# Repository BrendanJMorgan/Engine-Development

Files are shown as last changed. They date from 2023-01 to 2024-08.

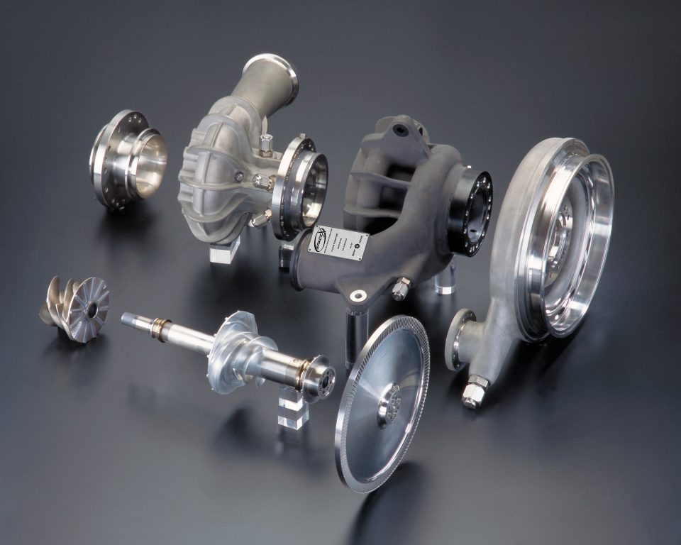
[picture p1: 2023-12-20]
Documents/Merlin-Turbopump-A-JPG1-960x768.jpg

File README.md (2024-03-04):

# Engine-Development
LOx-Ethanol Gas Generator Cycle Rocket Engine Analysis

This folder centers around designing a gas generator cycle rocket engine. By default the propellants are liquid oxygen and ethanol, though it should be fairly easy to change the code to other common propellants. The solidworks CAD reflects design parameters outputted by the MATLAB code. 

To use, open the main.m file and run. Engine target parameters can be adjusted right from this file. For example, target thrust, chamber pressure, OF ratio, and some basic dimensions for both the main combustion chamber (CC) and gas generator (GG) can be changed here.

The MATLAB code requires CoolProp integration to run. CoolProp is a python library with a MATLAB wrapper. The easiest installation method I know of can be followed from this video: https://www.youtube.com/watch?v=XvR10Fjph7U
The code also reuires NASA's CEAM to run, though this is already included in the folder so no further action should be required. NASA CEAM is approved for both domestic and international release.

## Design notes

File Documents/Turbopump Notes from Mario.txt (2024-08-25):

e pumps mostly
gillic textbook (julic? yulic?)
	roughness, specific speed
diffuser angles, stalling, loss vs angles
fuel inducer assuming impinging on leading edge
shrouding inducers is not that big deal, nor are somewhat wide tip clearances

ross (python library for rotordynamics)
pressurize seal with gn2, but two separated packing seals
zero leakage seal

x or o bearing arrangement

wave spring (soft preload better than hard preload)
tight tolerance on radial part of impeller (sealing) - 1 mm or less maybe
	other clearances can be wider
20-30% efficiency on turbine, maybe higher if load/power coefficient is lower

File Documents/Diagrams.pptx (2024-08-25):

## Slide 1

Spin Axis

rshaft

rinner

rrms

Flow In

reye

rexit

p1

p2

weye

Impeller Curve

Shroud Curve

p3

p4

wexit

Flow Out

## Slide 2

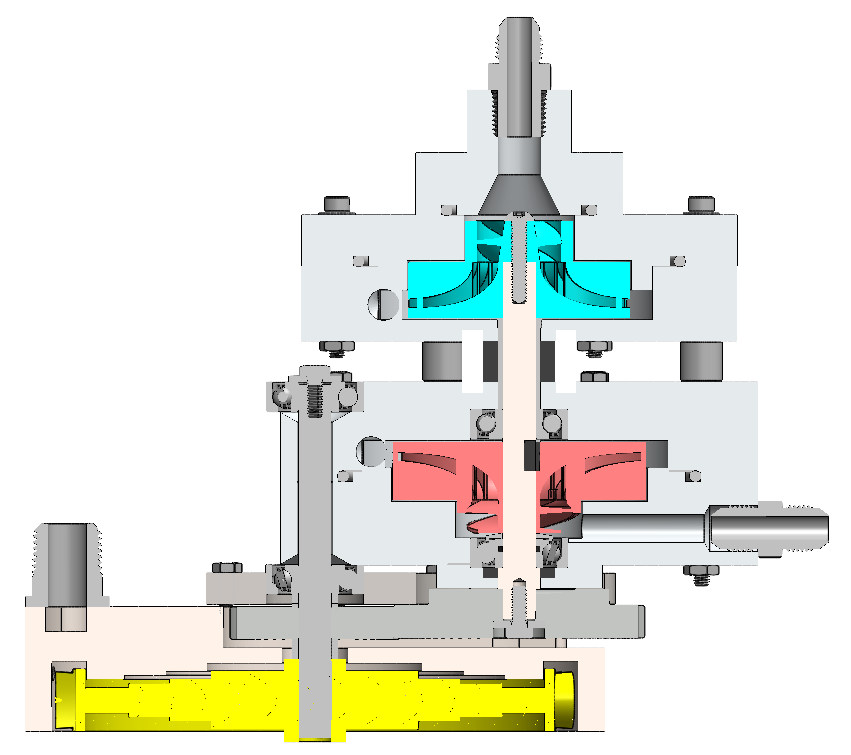
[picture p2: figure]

Ox Inlet

Oxidizer Pump

Bearings

Fuel Pump

Gas Inlet

Fuel Inlet

Manifold

Gears

Rotor

Turbine

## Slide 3

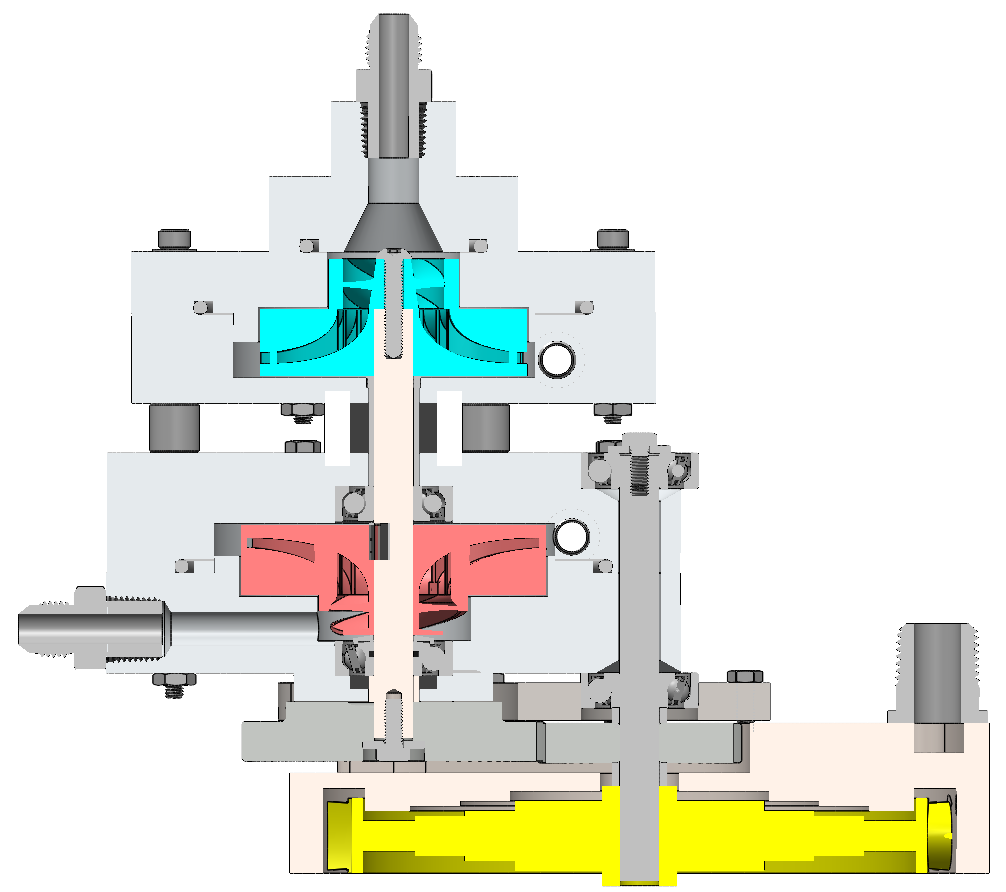
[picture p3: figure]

Ox Inlet

Oxidizer Pump

Outlets

Fuel Pump

Bearings

Fuel Inlet

Mounting Plate

Gas Inlet

Gears

Manifold

Turbine

Rotor

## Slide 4

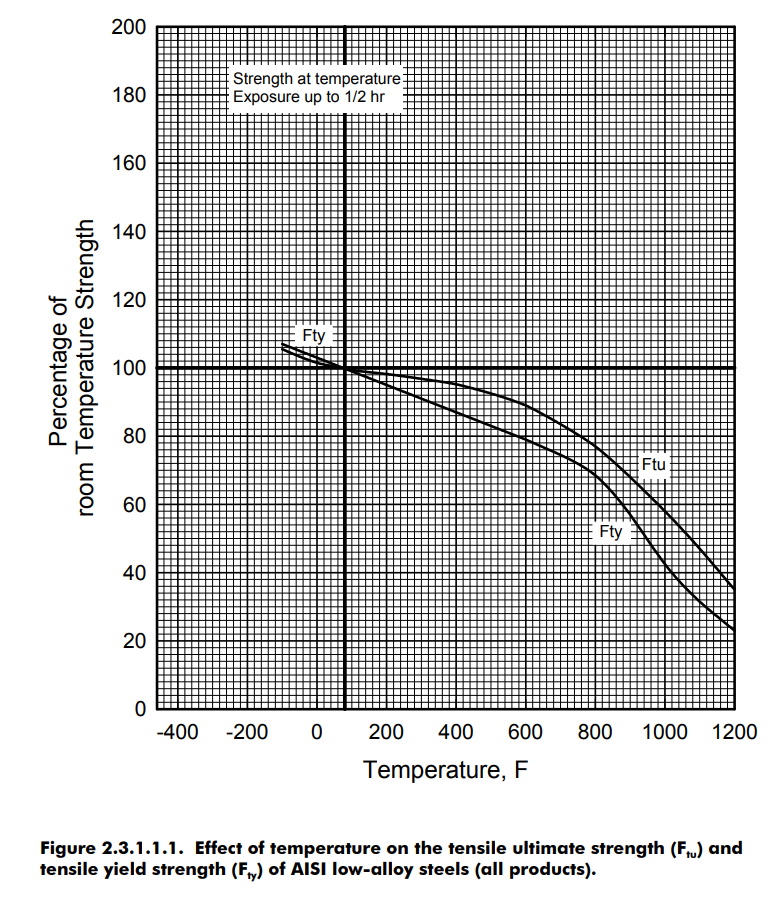
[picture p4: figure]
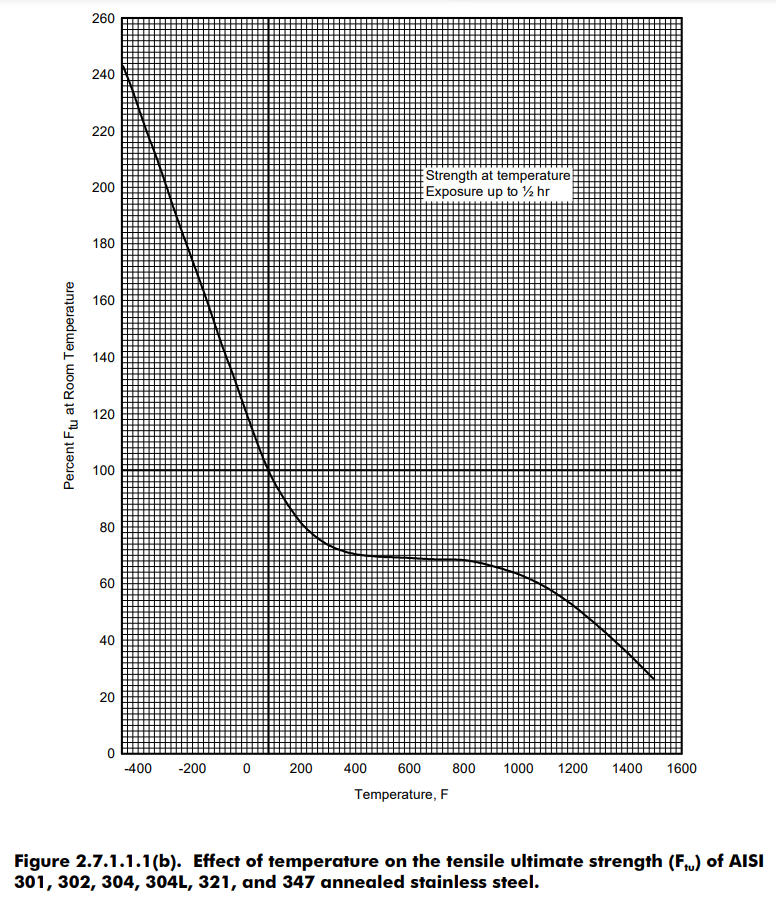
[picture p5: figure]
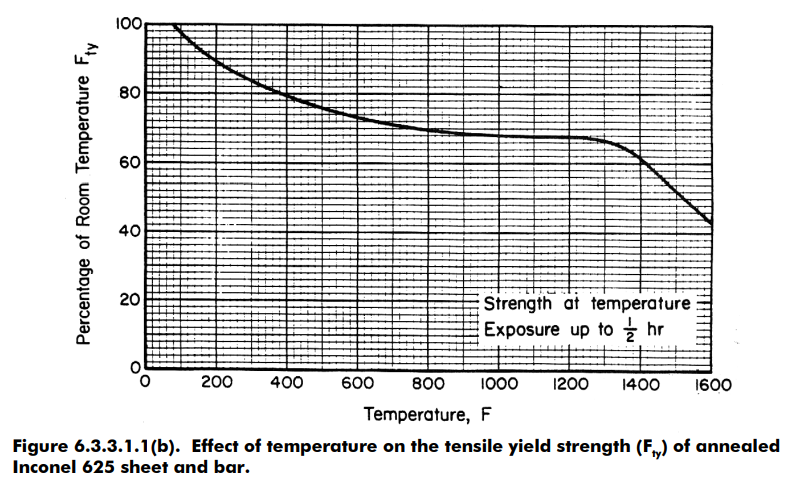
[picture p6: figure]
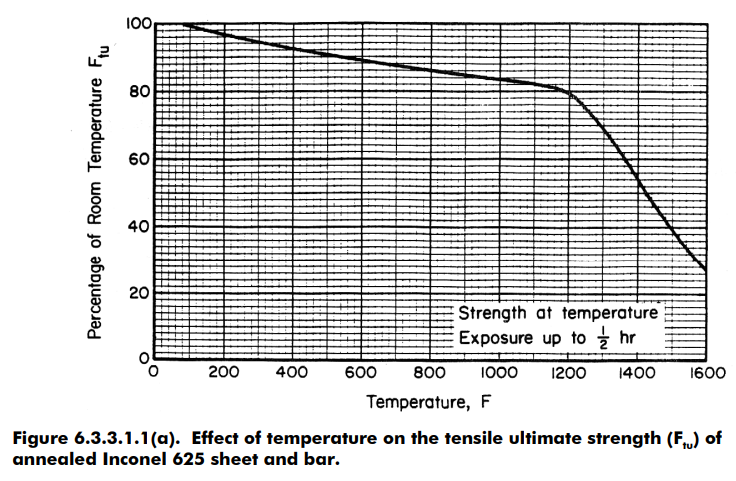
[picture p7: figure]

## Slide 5

rexit

p3

βoutlet

p4

p2

βinlet

reye

p1

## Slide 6

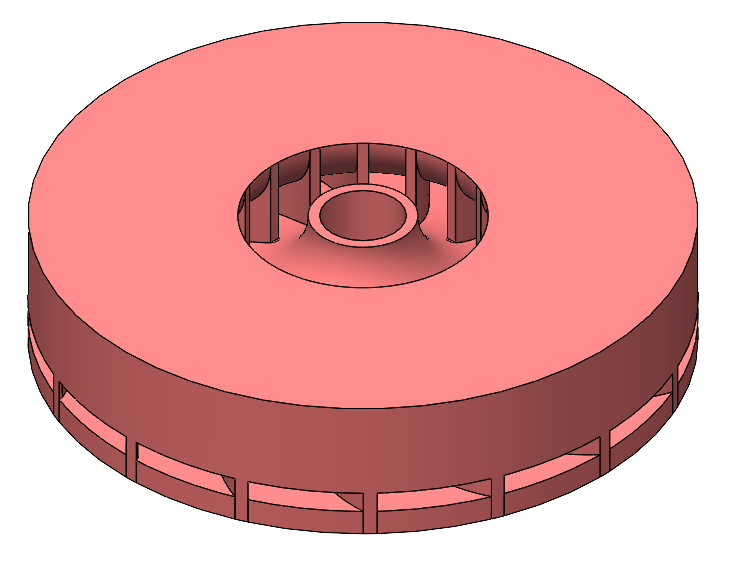
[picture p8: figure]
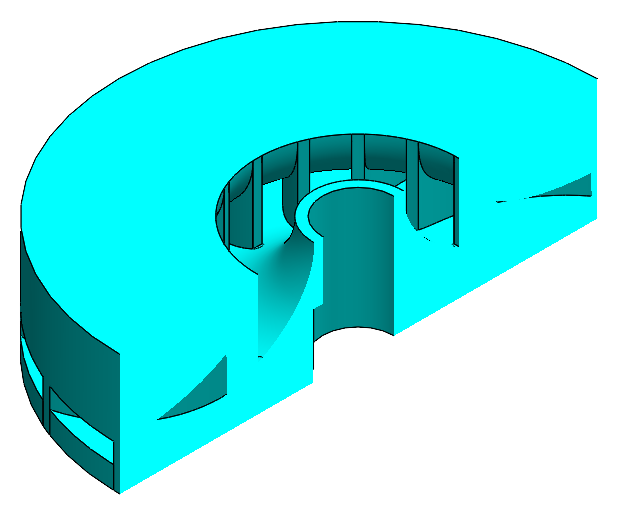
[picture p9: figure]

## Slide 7

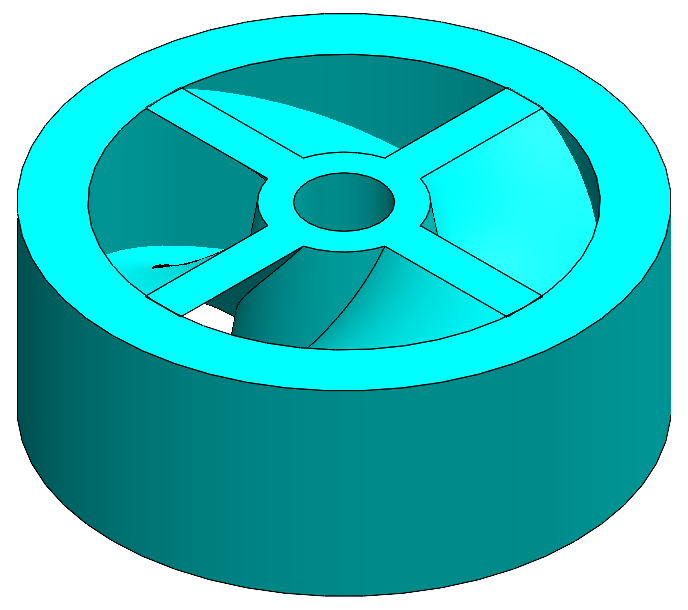
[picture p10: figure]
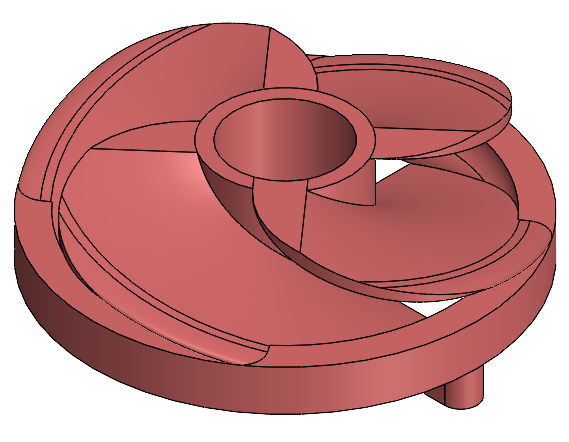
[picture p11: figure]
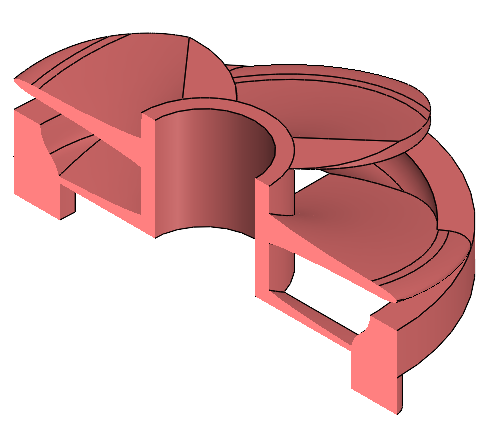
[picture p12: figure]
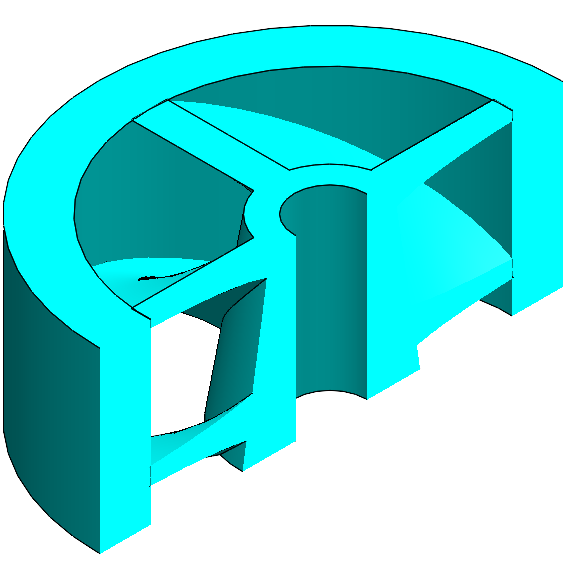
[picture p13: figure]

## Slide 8

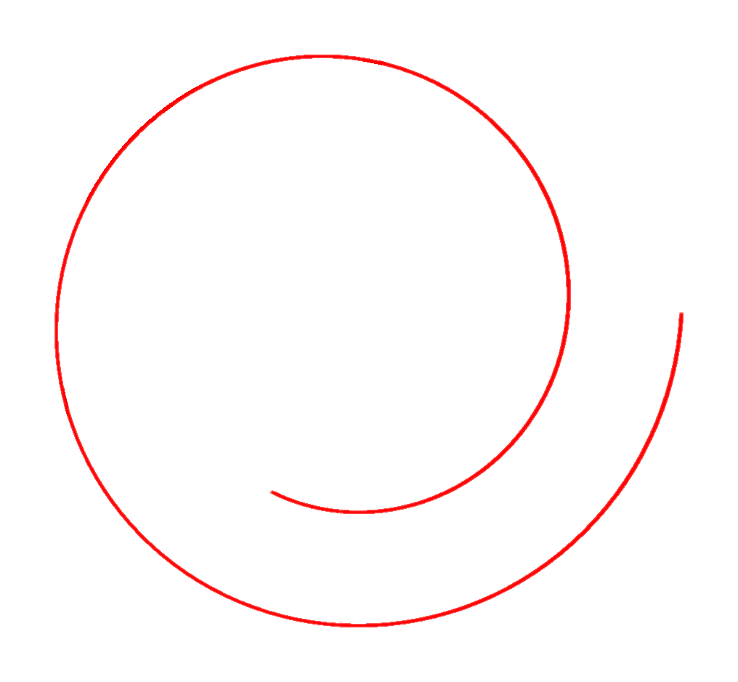
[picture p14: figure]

Impeller

routlet

rexit

Circular Cross Section, Aoutlet

Square Cross Section, Aoutlet

rtongue

ttongue

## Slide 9

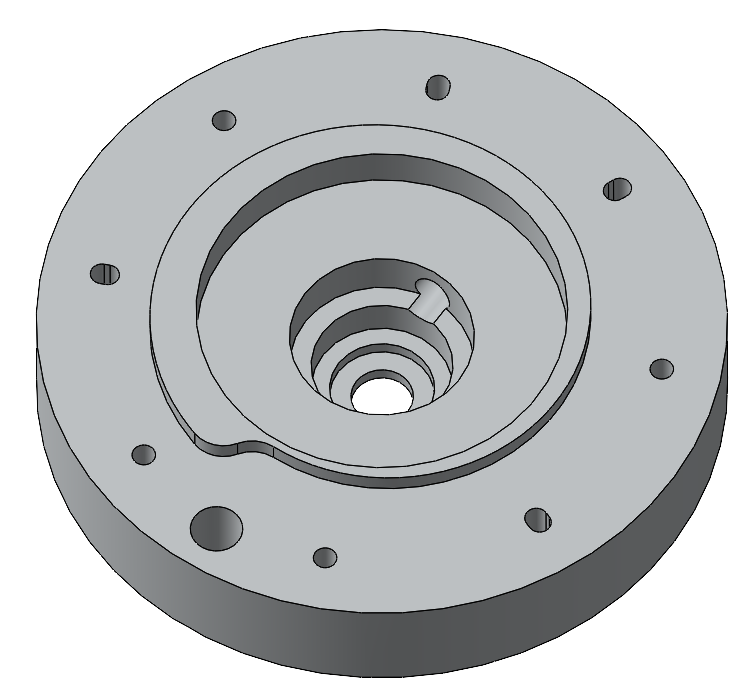
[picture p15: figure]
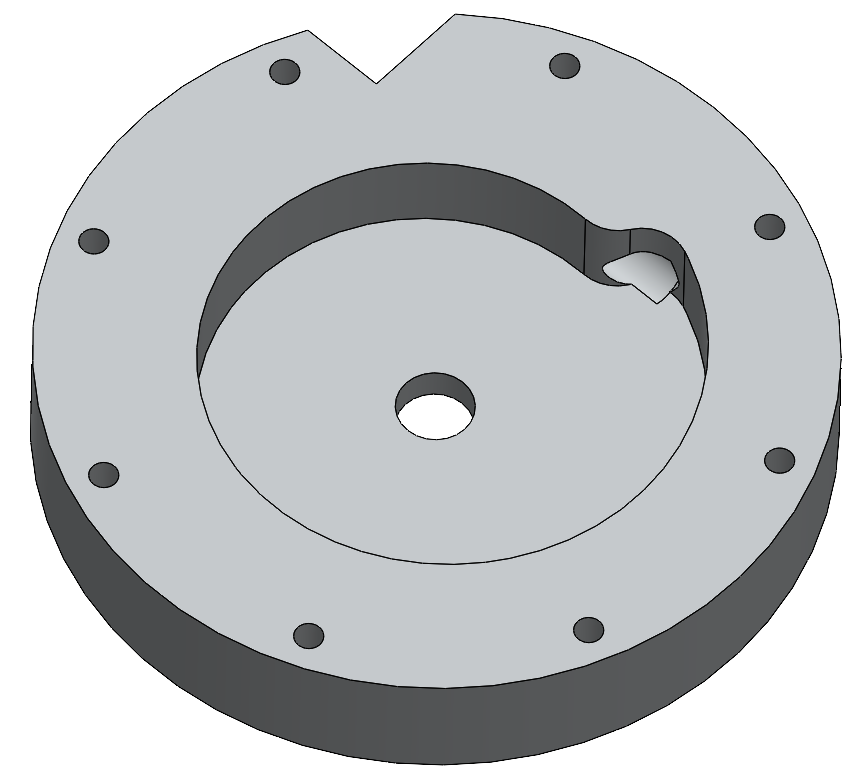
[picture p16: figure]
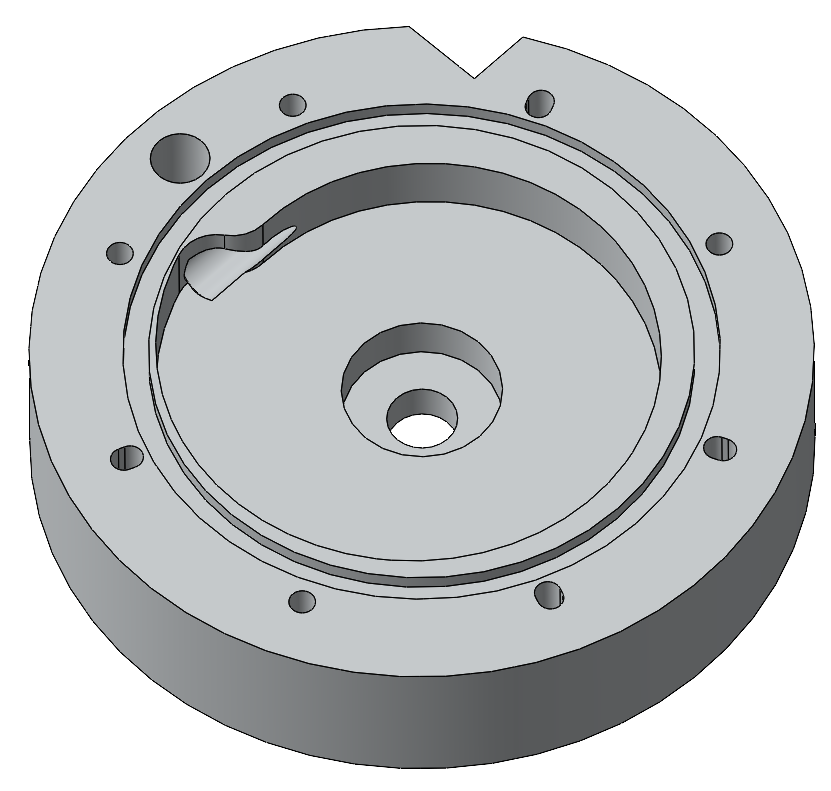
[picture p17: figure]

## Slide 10

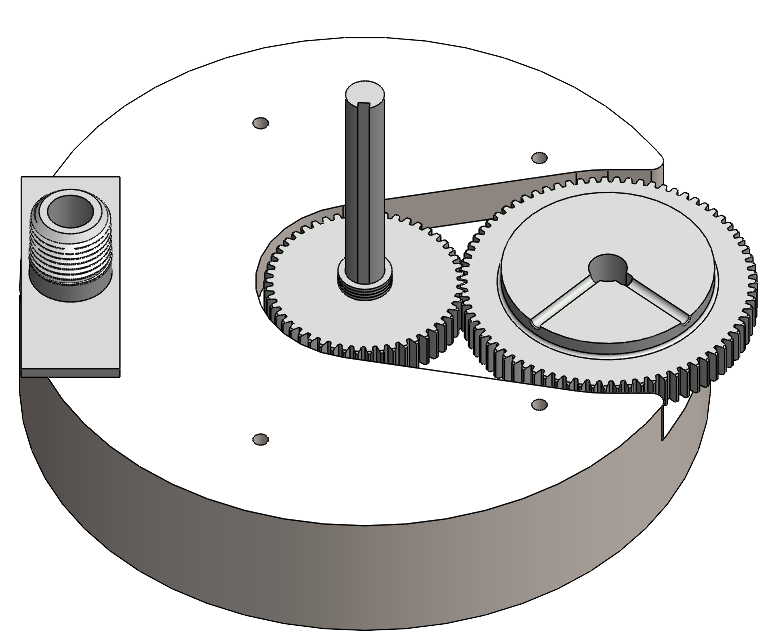
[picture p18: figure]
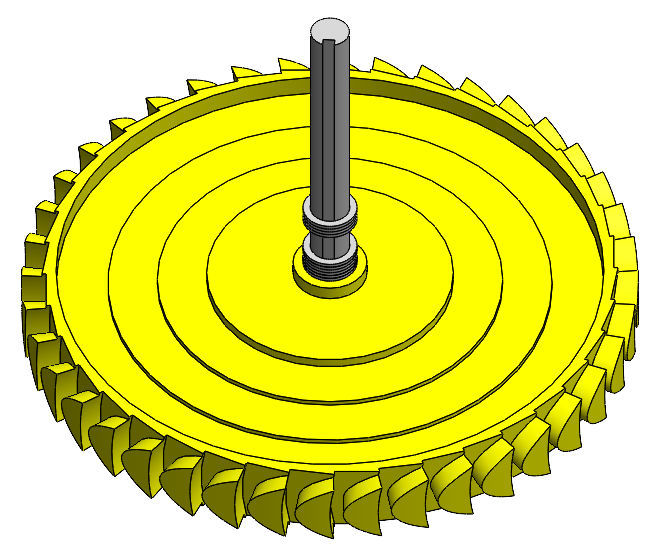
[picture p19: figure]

Gas inlet

Pump Gear

Turbine Gear

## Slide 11

Spin Axis

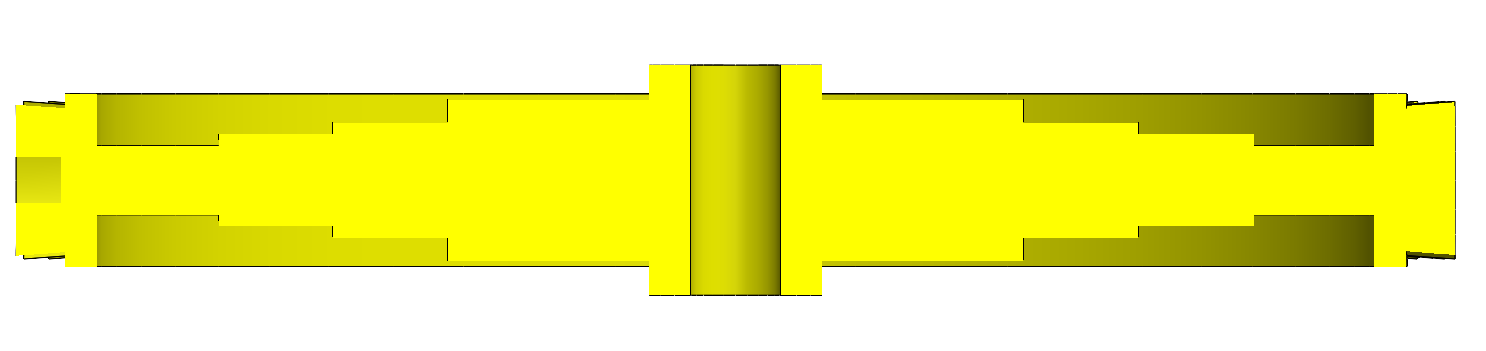
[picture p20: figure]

rshaft = 5 mm

rbase=2.875”

rtip=3.125”

rpitchline=3.00”

1.0”

0.7”

0.5”

0.4”

0.3”

0.75”

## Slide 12

Gas Manifold

θnozzle = 26.0o

dnozzle = 0.127”

θinlet = θoutlet = 13.7o

gap ~ 0.05”

lchord = 0.75”

ωr = 239.4 m/s

lpitch = 0.575”

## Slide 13

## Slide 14

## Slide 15

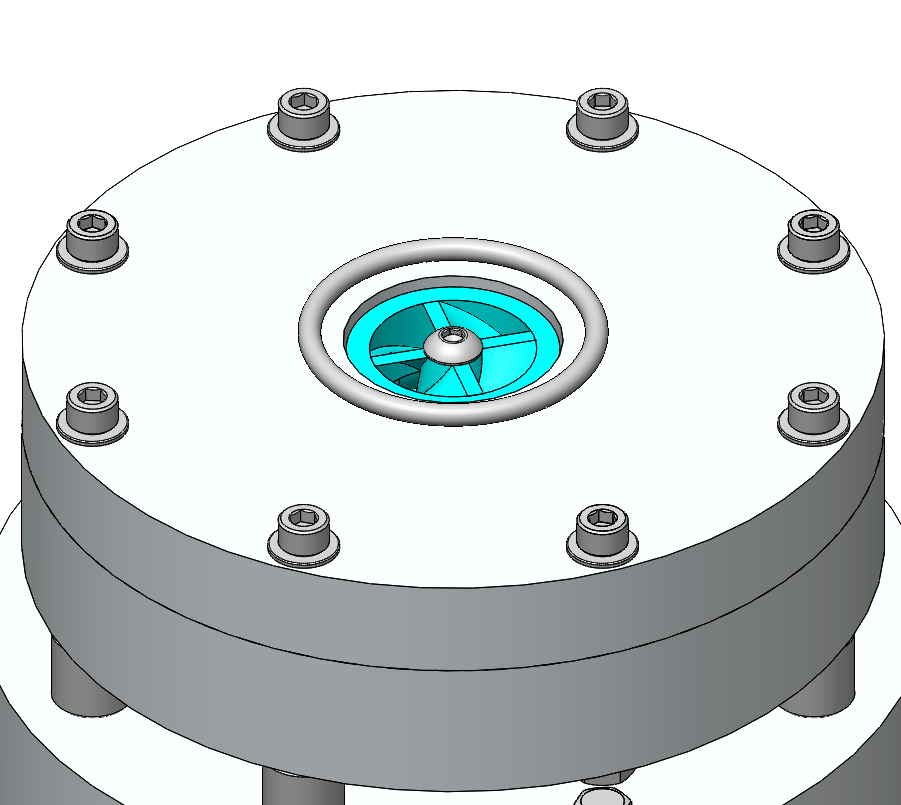
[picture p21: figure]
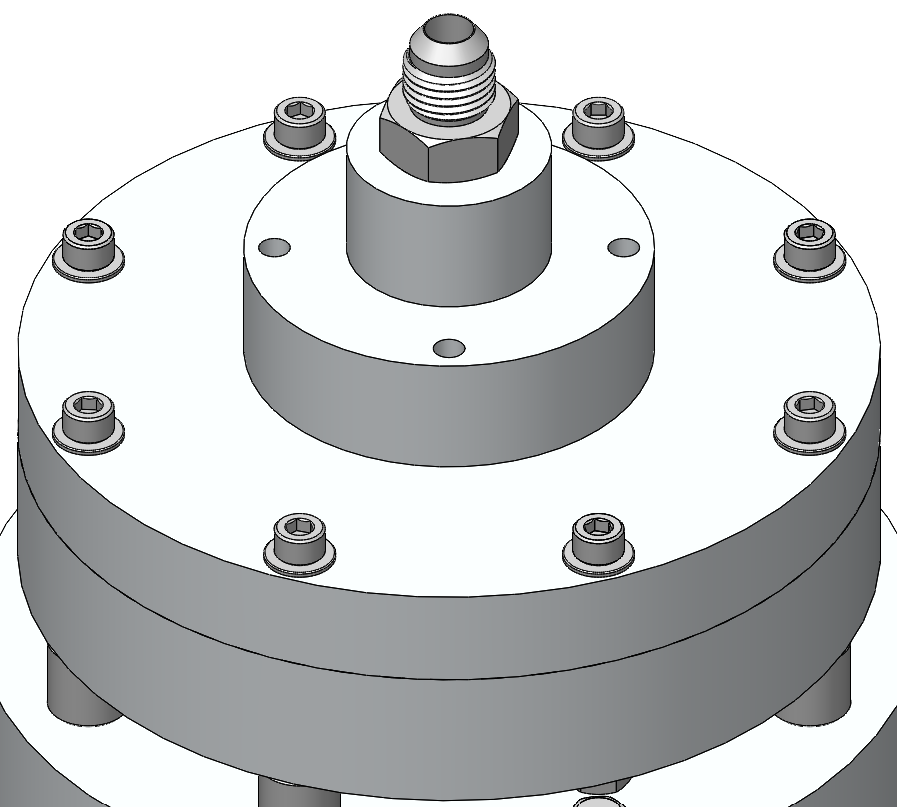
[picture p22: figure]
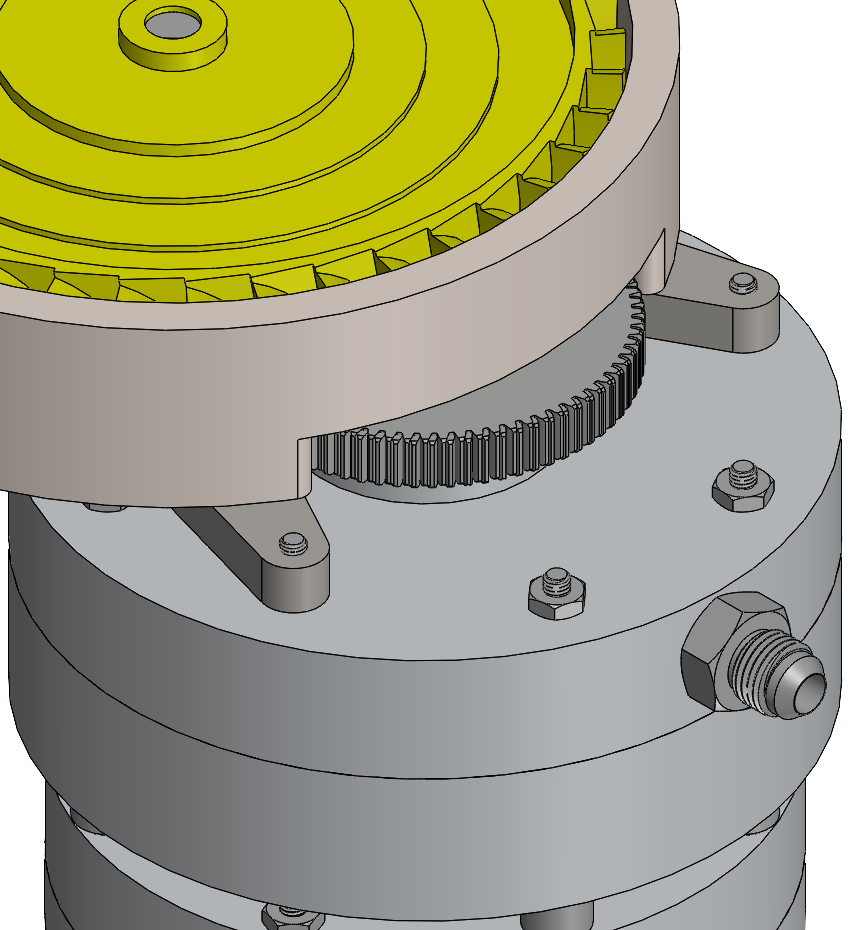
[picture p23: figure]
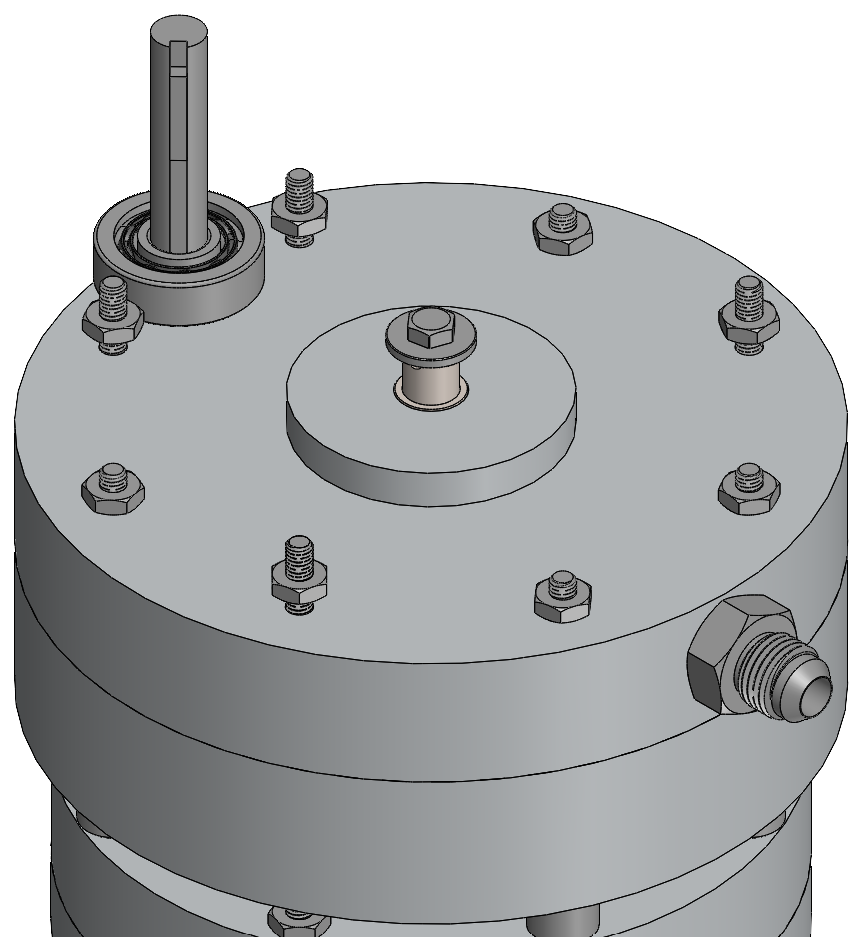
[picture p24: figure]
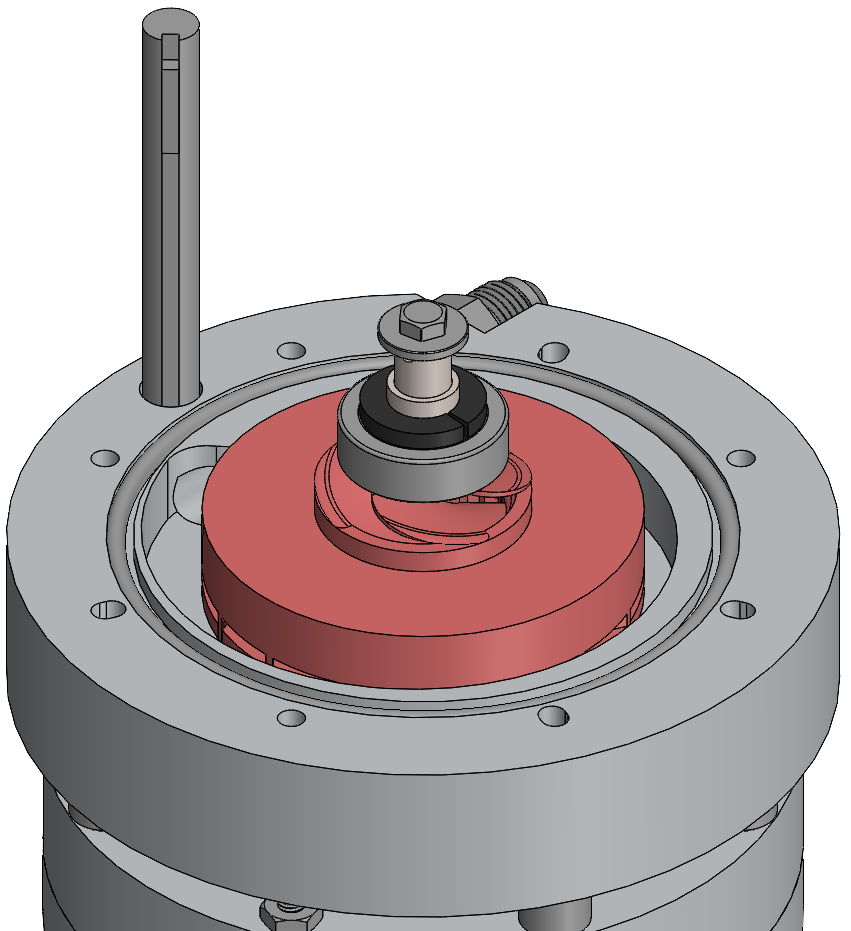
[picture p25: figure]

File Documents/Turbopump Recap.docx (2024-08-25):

Turbopump Testing Recap


Gas Turbine

Fuel Pump

Ox Pump

Summary

I (Brendan Morgan) designed/analyzed/machined/welded/integrated one complete turbopump, with serious design work beginning in September 2023 and the first test occurring the night of June 16-17 2024.

I’m calling the test a “spinflow” (turbine spin-up + pump waterflow). The turbine is spun up using pressurized nitrogen gas from bottles, and water is flowed though both pumps. The nitrogen gas is attempting to simulate a 0.557 kg/s (1017 SCFM) gas flow from a theoretical gas generator. The water is attempting to simulate a 4.5 kg/s flow of liquid oxygen and a 3.8 kg/s flow of 75% ethanol fuel. It is attempting to pressurize the oxidizer outlet to 428 psi and the fuel outlet to 448 psi.

Most design and analysis work can be found on my github and google drive (though some things are quite unpolished and unorganized):

https://github.com/BrendanJMorgan/Engine-Development

https://drive.google.com/drive/u/0/folders/1xzCn_89ndQEU2PsFcl7RbZjL71s8Y_nX

Wins and Strong Points

- The fact that it worked at all is surprising to me. I am stoked by the results of the test even though it significantly underperformed compared to the design goals.
- Little to no noticeable water leakage around any of the seals, barring a little dribbling on one side of the fuel pump. This was expected and discussed later.
- No noticeable structural damage on the pumps or turbine.
- Packing seals performed well as far as I can tell, though they should be inspected when the turbopump is taken apart later.
- Turbine seemed pretty balanced for the relatively minimal work I put in to doing so.

Main Issues


Turbine Manifold

Pump Shaft

This fastener was not present on actual hardware

Pump Gear

Fuel Inlet

Likely Air Flow

1) Fuel pump flow was almost nonexistent compared to lox pump. I am pretty sure this is because it was not properly sealed along its shaft, on the side close to the inlet and inducer. This is really the only relevant difference I can think of between the two pumps that could cause this. It could have been aspirating a lot of air into its inlet, more than water – maybe there was a high-pressure stream of air coming out the outlet but it’s impossible to know from the video.

My intent was to put packing seals in the pictured gap, but because it rests against the bearing it jammed the balls when I tried this; I was not able to rotate the shaft by hand at all. I opted to not put any seal at all here because of lack of time and naively hoping that the clearance between the shaft and hole was small enough to kinda seal it. I knew water was going to leak out before the test started (which it did at a very slow dribble that doesn’t really affect anything), but I hadn’t thought about the fact that air would leak in during the test, in the opposite direction.

So that’s a simple design oversight – I’m thinking now I may be able to correct this by adding a small, specifically dimensioned washer of some kind that separates the bearing from the packing seals, and adding a packing seal back in. Or I may switch the open ball bearing to a sealed ball bearing and take the hit on max shaft RPM, especially since the real speed isn’t getting close anyways. This test did demonstrate that packing seals work (at least to some degree), because there was a packing seals separating the fuel and lox pumps. If they did not work then the lox pump would have been aspirating air from the fuel pump and had similarly anemic performance.

2) The first test spun great, overcoming any friction, but subsequent tests ground to a halt. We could hear (and verified from videos) that the turbine would begin spinning up for a few seconds at most and then slowed to a stop. After reapproaching, I would try to spin the turbine by hand and each time it would feel caught until I worked it around a little bit and it would start spinning freely again. Some parts (especially the gear and fuel pump casing) were slightly warmer than the other parts. To be clear, everything was quite cold from water splashing around and adiabatically expanded nitrogen gas flowing through the system (both the dome regs and nitrogen bottles were fully iced up on their surface), but those parts were close to more room temperature.

So I think it’s pretty clear the issue was a sudden spike in friction when it started spinning, and one that would not have appeared in the first test. In light of this I am pretty sure the issue is the pump gear sliding up along the shaft and coming in contact with the steel of the turbine manifold. A couple days ago I had angle grinded the pump shaft shorter and forgot to redrill and tap a bolt hole on its end which was to be used for the retention of that gear. So the gear was just friction fit axially onto the shaft (it still had a shaft key for rotation/torque so that wasn’t an issue). I didn’t fully remember this until integration was almost done, but I naively rationalized the fit was tight enough (I had to hammer it on originally, it was close to an interference fit probably) that I could leave it so I didn’t have to take it all apart and put back together (which can take hours sometimes). Last night I noticed what was originally a tight fit had gotten progressively looser from fiddling around with the system. So about an hour or so before the test, I was able to place some 5 minute epoxy on the shaft around both sides of the gear (using a 3/32” welding rod, that’s how thin the gap was). I think this epoxy job was enough for the first test to work. But because everything got quite cold and wet, the epoxy probably shattered and/or washed away at some point before the second test. Then the pump gear slid down the shaft during that test and the gear started rubbing on steel and brought the whole thing to a halt.

3) The rotation rate was way too low, so the whole system underperformed. Looking at the audio spectrum, there is a strong peak around 3750 Hz * 60 s/min * 40 blades/revolution = 5625 RPM; the target for turbine speed is 30,000 RPM (and pump speed should be 20,000 RPM). This is almost certainly mainly because the nitrogen flowrate was much too slow. Target was ~1000 SCFM, but a rough estimate of the actual rate would be 2 bottles * 230 SCF / ~2.5 min = 184 SCFM. Turbine speed is theoretically a linear function of gas mdot, which completely tracks: 1017 SCFM / 184 SCFM * 5625 RPM = ~31000 RPM. So I think it is valid to say there is no speed problem with the turbopump itself, only the nitrogen feed to it.

I suspect the primary issue is the size of the orifice built into the bottle itself. I think it is possible a smaller effect might be a limitation of the dome reg when it gets quite cold; both regs were entirely iced up on their surface at the end of the test. I don’t think pressure loss through the feed system is a major issue because Alex did a test of this and there was very little difference between the supply reg pressure and the pressure downstream of the dome regs, and everything is a straight shot from there down to the manifold orifices without opportunity for significant losses.

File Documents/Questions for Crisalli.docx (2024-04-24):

Questions for Crisalli:

- Is this shitty casting ok lol
- Should I prioritize high speed or cryogenic compatibility on my bearings? Ball or sleeve?
- Should the bearing be immersed in the pump or behind a seal?
- How important is shaft straightness? Do I invest in precision tolerances?
- Do I need a bearing on the lox side?
- Do I need thrust bearings?

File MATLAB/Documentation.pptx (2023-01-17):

## MATLAB for GG Cycle Engine

Brendan Morgan

## Getting Started

- All files should be in the same folder
- Must download CoolProp for MATLAB
  - Requires an installation of Anaconda for Python
  - Instructions here: https://www.youtube.com/watch?v=XvR10Fjph7U
- Must request CEAM from NASA software catalog and download to same folder as other files
  - Request here: https://software.nasa.gov/software/MFS-33320-1
- Run “main.m”

## Overview and Motivation


- Model a gas generator cycle engine with sufficient detail to inform CAD, FEA, and CFD models with few to no other calculations
- Fuel is ethanol (proof can be varied) and liquid oxygen. Combustion chamber and gas generator are intended to run fuel-rich, however the OF ratio of both can be modified to any value.
- Calculations take a “top-down” approach: the final desired results are entered as inputs (e.g. thrust, chamber pressure, OF ratio), and then the script works backwards through the system and outputs requirements to achieve the desired results (e.g. mass flow from tanks, turbopump efficiencies)

## main.m

- First section is all inputs. All these numbers can be safely modified without breaking the program; however, some configurations will not be physically possible and error messages will be thrown (e.g., requested chamber pressure is too high and needs a dangerously high contraction ratio)

## combustion.m

## exhaust_flow.m

## thermal_balance.m

## pump.m

## gas_generator.m

## Acknowledgements

- NASA Software Catalog
- CoolProp
- Cryo-Rocket.com by Brian Brady

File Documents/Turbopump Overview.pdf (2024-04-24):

# Context

- Eventual goal is to feed 3000 lbf, 400 psi engine, 1.4 OF, LOx & 95% ethanol
- Higher thrust than team so not pumping tiny mass flow (I can only machine parts so small…), other properties similar because messing with these is not my project goal.
- Goal is to not pressurize tanks whatsoever.
- Reducing mass is very low priority for me, my goal is to hotfire a concept not launch a rocket.
- Total (CC+GG): 4.34 kg/s lox, 3.15 kg/s fuel
To Gas Generator: 11.6 g/s lox, 57.8 g/s fuel
- Initial tests will be powered off an N2 bottle like you suggested.
- I do not have a CAD design for a GG yet, but my concept is:
- 400 psi, 1360 F, 0.2 OF
- Side-Outlet Reverse flow design, ¼” steel construction with 6061 injector
- Central lox orifice flanked by four fuel orifices impinging on it and another four impinging on the wall (for film)
- Estes motor, mounted so exhaust blows across cylindrical GG, parallel to injector face, then proceeding out GG outlet into turbine manifold. Dual purpose: igniting GG and spin starting the turbine in the meantime. Unsure about potential for clogging injector and/or turbine nozzle holes.
- I plan on doing a structural, modal, and thermal FEA for the whole thing
- Large reason I’m contacting you now is to get feedback on design before I launch into this analysis too far.
- I’ve been working on this on and off for a bit over one year. Most of that time has been spent developing an all-encompassing MATLAB model for the whole cycle, not just cadding the turbopump (I did most of that in the past month). Thank you for any and all feedback you may have.
- I come from primarily a structures background, not a propulsion one, so don’t hesitate to point out errors that might seem obvious. There are probably a lot of gaps in my knowledge on the basics of plumbing/fluids/thermal
- I have my code/cads/analysis here if you happen to want to look, but I definitely don’t expect you to do that.
- https://github.com/BrendanJMorgan/Engine-Development

## Lox In


## Fuel In

## Fuel Out

## Lox Out

Gears 100:25 Teeth
Module 1
80,000:20,000 RPM

Keyed Shafts 10 mm OD, 304 SS, Tapped Ends 10-32

GMN Angular Bearings 15oContact
https://www.gmnbt.com/products/bb-s-61800-c-ta-angular-contact-bearing/ (https://www.gmnbt.com/products/bb-s-61800-c-ta-angular-contact-bearing/)

Air gaps for thermal, may
put insulation sheets

## Turbine Manifold

## Hot Gas In

# Fuel Pump

## 20,000 RPM, 4.99 ft-lb


## 6” Casing OD

Designed Impeller & Volute using Pump Handbook Inducer not fully designed yet, CAD is a placeholder

## Consumes 14.8 kW (71.7% hydraulic efficiency)

Angular Bearings Preloaded, pushed outwards
Turbine Shaft Mount

PTFE Spacer +
CF Packing Seals

# LOx Pump

## 20,000 RPM, 5.22 ft-lb


10-32 clamps the stack
onto bearing

## Consumes 14.2 kW (71.4% hydraulic efficiency)

PTFE O-Rings

PTFE Spacer (Under Compression), surrounding CF packing seals

## 5” Casing OD

3D printed pla models
of lox and fuel casings
with my hand for scale

Casings, Impellers,

## Inducers are all aluminum per your recommendation

# Turbine

## 80,000 RPM, 2.69 ft-lb


Structural steel plate
for attaching to pumps

Inlet
from GG

Three
Nozzles

Graphite
Gasket

Unsure how to size
manifold cross section

Each nozzle has 0.088” throat, 15⁰ half angle divergence. 45o absolute angle. Plan on drilling out with a 2.2 mm bit.
I am concerned they are too tiny (i.e. hard to tolerance) but my gg’s mdot is so low I don’t know how to make them much bigger

Rotor is 3/8” 304 SS blisk. OD 5.8”, pitchline radius 2.5” Each blade gap formed by two end mill cuts at 26.6o

(relative flow angle to vertical)

10-32’s clamp rotor
stack onto bearing

Ceramic bearings
preloaded (pulled
together). Is ceramic
good for the heat load?

CF Seal

## Supplies 30.5 kW (5% loss on gears?)

## Everything metal here

is 304 stainless.

# Casting


In November before I talked to you I tried sand casting my impellers in aluminum bronze.

Used greensand – I halved playsand and halved bentonite clay, with cornstarch for nonstick

Came out pretty terribly haha
In theory this is two open impellers and two shrouds connected by sprues…

Casting In early January I tried again, with investment per your recommendation and A357. (Though I ran out and mixed some 6061 in as well)

Vacuum chamber with investment. This stuff:
https://www.amazon.com/Premium-Jewelry-Making-Casting-Investment/dp/B07SXD7PW9 (https://www.amazon.com/Premium-Jewelry-Making-Casting-Investment/dp/B07SXD7PW9)


PLA burnout with charcoal. Actually kinda worked but I think it may have led to the investment crumbling internally


I sprued the PLA prints with hot glue sticks inside soup cans

## Results were slightly better than the first time but still pretty bad. At this point I’ve given up for now and plan on outsourcing my impellers and inducers to be metal 3D printed, then return to

trying casting at some later date.


## That is, unless you see major errors I could fix that would lead to much better results?

# Major Questions

- I welcome feedback on anything amiss you see, This is just what I have been thinking about most.
- Seals are a top concern of mine. You suggested labyrinth seals, though it is quite hard to find a place to buy a small quantity. I opted for carbon fiber packing seals (https://www.mcmaster.com/9437K4/). They are the highest speed contact seals I could find anywhere at 4400 feet/min. My pump shaft is 2060 ft/min so I plan to use those on it, but my turbine shaft is 8250 ft/min. I’m considering using them anyways and if they burn off, so be it because it seems unlikely to me that hot gas would preferentially travel from the blades inward and up the shaft, and even if they did my turbine shaft is completely decoupled from the pumps so the hot gas can’t really damage anything (other than just heating up the pump exteriors somewhat).
- Is this valid or am I off base here and should continue searching for non-contact seals?
- As it stands there are no bearings at all on the lox pump; the shaft is cantilevered off the two fuel side bearings. This is because it is quite hard to find something cryo rated at my shaft speed. The two fuel bearings are preloaded (they are being pushed away from each other) so I’m hoping that will provide good stiffness for this and the 100 tooth gear, which is also cantilevered though with a short moment arm.
- Would this probably be stiff enough in your experience?
- I have no idea what my clearances should be. In my CAD right now there's about 10-20 thou around the impellers on all sides, should I go higher?
- Same questions on the turbine shaft, which is preloaded oppositely (bearings pulled toward each other)
- Is there much advantage of ceramic bearings over stainless steel ones? GMN has both for my size but it’s unclear what would best apply to my case.
- I went with a geared design because otherwise my rotor has a ~20” pitchline radius, which is prohibitively large for me to buy, machine, and integrate. Though I have little experience with gears.
- Is gearing at these speeds practical in your opinion/experience?
- I chose spur gears so I didn’t have to deal with thrust on a helical. Should I be concerned about excessive vibration and/or wear?
- Should I be concerned about the effect of turbine heat load on the lubrication?
- This is more minor but I’ve often heard gears should have a coprime number of teeth. Is this a real concern or a nice-to-have? The 100 and 25 tooth gears were the most practical I could find from KHK.

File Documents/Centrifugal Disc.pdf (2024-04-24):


## Calculation of the Hoop Burst Speed for Rotating Discs

In high speed turbomachinery, the discs which support the blades are highly loaded structural members. The kinetic energy in discs is considerable and whilst designed to avoid burst failure, if this occurs the surrounding structure is often not strong enough to contain the disc fragments, e.g,:

http://www.telegraph.co.uk/news/2016/10/30/american-airlines-plane-engine-flung-debris-in-rare-risky-failur/

The primary loading faced by a turbomachinery disc is that induced by rotation. This includes centrifugal self-loading and a radial load at the periphery due to the centrifugal loading of the attached blades and such loading induces stresses in the disc that are proportional to the square of the angular velocity . Although, the detailed design of a disc might include

consideration of a range of potential failure mechanisms like, for example, low cycle fatigue induced by thermal and mechanical cycling, the basic disc shape is governed by the basic strength requirement to resist circumferential or hoop burst. Whilst hoop burst of a rotating disc is a phenomenon involving material plasticity and large displacements and strains, a rather simple approach, based on a linear-elastic analysis of an axisymmetric model of the disc, has been shown to provide sufficiently accurate predictions of the burst speed for the purposes of initial design. The method is attributed to Robinson, [1], and is discussed on p50 of Chianese Stefano’s 2011 Master’s thesis, [2].
Hoop burst involves the circumferential or hoop stress - which varies over the generator plane of the disc. Robinson’s method requires the area weighted average hoop stress -

to be calculated for a given angular velocity . The angular velocity to cause the disc to burst is given in terms of the ultimate tensile strength, -

, of the material.  ; where the; average hoop stress is given by -; and A is the; area of the disc generator; plane.; Parallel; Tapered; Axis of Rotation; =210GPa; - =1000MPa

Figure 1: Generator planes for the axisymmetric finite element analysis of two rotating discs

The Challenge
The reader is asked to use his/her finite element system to determine the angular velocity to cause the two discs of Figure 1 to burst based on a UTS of 1000MPa. For this study, no radial loads due to blades are considered. For the parallel sided disc the theoretical solution based on the Lamé equations can be used for software verification – see for example reference [3]. The second, tapered, disc has no theoretical solution and solution verification will need to be used to ensure that the mean hoop stress calculated by the axisymmetric finite element model has converged sufficiently.

### Raison d’être for the Challenge

A great virtue of finite element (FE) analysis is that once software and solution verification have been carefully undertaken then the engineer may freely use a finite element model to explore in more detail the mechanics of a design and therefore put under scrutiny the design rules adopted for his/her component of interest.

This challenge puts the empirical design rule of Robinson for the prediction of burst in rotating discs under such scrutiny. The process uncovers some interesting facts about the finite element

Inner radius = 0

Outer radius = 0.1m

Inner thickness = 0.03m

Outer thickness = 0.03m and 0.015m modelling of such components and also brings into sharp focus the inadequacy of the empirical design rule which is still used to this day!

The Robinson approach relies on an empirical correlation between the average hoop stress at burst and the ultimate tensile strength of the material. A rational basis for this can be developed by considering the theoretical solutions for a rotating disc with parallel sides.

Average Hoop Stress from Statics
The average hoop stress for a disc can be calculated by considering the statics of half of a full disc as shown in Figure 2.


Figure 2: Average hoop stress from disc statics (=1000rad/sec)

### Theoretical Elastic Solution

Lamé theory provides an exact linear elastic solution for thick-walled pressurised cylinders where the ends are either constrained from longitudinal displacement (plane strain) or are free (plane stress). It was illustrated in NBC03 that even if the ends are free, as the length of the cylinder increases the state of stress at the central axial plane tends towards that of plane strain due to the self-constraint of the material. Whereas for pressurised cylinders the loading is through applied (radial) boundary tractions, for a rotating disc, the loading is a radial body force which increases linearly with radius. In contrast to pressurised cylinders, which are usually long in comparison to their diameter, discs often have an axial length which is comparable to their diameter. As such the axial length is generally insufficient for a complete plane strain situation to develop at the centre of the disc and thus a plane stress assumption is more appropriate.

< is the disc thickness (into; the page in this figure)

Figure 3: Equilibrium, constitutive (plane stress) and compatibility conditions for a rotating disc

Using the equilibrium, constitutive and compatibility conditions shown in Figure 3 together with the static boundary condition of zero radial stress at the outer radius, the stresses for the linear elastic case are as given in Equation (1).

Hoop | Radial

Elastic

8

[3 +

− 1 + 3"

] -

$ 3 +

8

− "
(1)

The variation in stress is quadratic with radius as shown in Figure 4. The radial and hoop stresses are equal at the centre of the disc and, as there is no radial load applied at the periphery then the radial stress is zero at the outer radius. The average hoop stress of Equation (2) is calculated by integrating the elastic hoop stress of Equation (1), over the area of the disc generator plane and dividing by the area.

Average Hoop Stress | -

3

(2)

The average hoop stress for the parallel disc at =1000rad/sec is 26MPa which agrees with the value

obtained from statics in Figure 2. The maximum stress occurs at the centre of the disc where the radial and hoop stresses are equal at just over 32MPa. As such, the elastic limit speed, the speed at which the first point in the disc reaches the yield stress, is as given in Equation (3) for the parallel sided disc.

Elastic Limit Speed (Theoretical) | & 1000(

1000

# 32 5590.2 rad/sec

(3)

It is realised that in Equation (3) the UTS has been used as the yield stress. This is common practice in many engineering industries and the appropriateness, or otherwise, of this substitution will be discussed later in this article. It is noted also that sometimes the ‘flow’ stress is used which is generally taken as the average of the yield and ultimate stress values.

Equilibrium:

− -

$ − "

4-
$

4" "

Constitutive: | 5

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
Compatibility:

"

46$
4" −

4
4" :"

46
4" ; 0

### Theoretical Plastic Solution

A plastic solution for the rotating disc may be obtained through the lower bound theorem of plasticity which requires an equilibrating stress field that nowhere violates the yield criterion. The linear elastic solution is an equilibrating stress field and can be considered as a particular solution for the plastic problem. A hyperstatic or self-balancing stress field may be added to the particular solution so as to maximise the load carrying capacity of the disc and provide a total solution that does not violate the yield criterion. A hint has already been given regarding the nature of the total solution at collapse in the empirical studies by Robinson where he showed a good correlation between the average hoop stress at burst and the ultimate strength of the material. As such the hoop component of a candidate hyperstatic solution would be the difference between the average hoop stress and that of the particular (elastic) solution as shown in Equation (4).
Hyperstatic hoop stress | -

= -

− -
| (4)

The corresponding radial component of the hyperstatic solution can be obtained by substituting the hoop stress into the homogeneous form of the equilibrium equation, i.e., the form with no loading term, and also satisfying the static condition of zero stress at the outer radius as shown in Equation (5).

Hoop | Radial

Hyperstatic

=

24

1 + 33"
−
$

=

24

1 + 3"
−
(5)

The various parts, particular and hyperstatic, of the total solution are shown, as a function of radius in Figure 4 together with the elastic and plastic stress as they lie within the Tresca yield criterion.


The Total stress is the sum of the Particular and the Hyperstatic stresses and these are shown in the left-hand figure for a speed of 1000rad/sec. The right-hand figure shows the Tresca yield criterion at 1000MPa yield stress. The total stress at the elastic and plastic limit speeds are plotted on the diagram as yellow lines with the top point corresponding to the centre of the disc (where radial and hoop stresses are equal) and the bottom point to the periphery where the radial stress is zero.
Figure 4: Development of a theoretical lower bound solution

The plastic theory outlined above follows closely that of reference [4], but has been cast in the form of an equilibrium analysis. The plastic limit speed is given in Equation [6].

Plastic Limit Speed (Theoretical) | ? 1000(

1000

# 26 6201.7 rad/sec (6)

Thus, for the Tresca yield criterion, all points of the disc are at yield and the proposed lower bound solution is then also the theoretically exact solution, i.e., the disc cannot take any more load. The increase in disc speed from the elastic to the plastic limit speed is just over 10%:

Plastic/Elastic Limit Speed Ratio (Theoretical)

?
&

6201.7
5590.2

≅ 1.10 (7)

The two preceding sections have developed the elastic and plastic solutions for parallel sided rotating discs. This theory shows that for a rigid, perfectly plastic material which obeys the Tresca yield criterion, the average hoop stress calculated from an elastic solution can be used to predict the burst speed of a parallel sided rotating disc.

### Finite Element Models

The geometry of a disc has many forms of symmetry that may be utilised in a finite element model. A solid model might be used of the complete disc but as there is no variation in the stresses in the circumferential direction a cyclic sector model could be used with symmetry boundary conditions applied to the sector faces. In a similar manner, a sector model using planar elements might be used. The most appropriate model though would be an axisymmetric one in which a generator plane is meshed. Such a model would show any variation in the two main stress components (radial and hoop) with axial position. Additionally, as the disc has a central plane of symmetry normal to the axis of rotation it is only necessary to model half of the generator plane as illustrated in Figure 5.


There are three possible finite element models that might be used, solid, planar or axisymmetric. The axisymmetric model is chosen as it will show the axial variation in the stress and involves no approximation of the circular arc – even higher-order elements are unable to approximate an arc exactly. As the disc is symmetric about a central plane normal to the axis of rotation only half of the generator plane needs to be modelled and the addition of symmetry boundary conditions on this plane of symmetry eliminates the axial rigid body displacement. It is worth pointing out that the possibility of modelling the same problem with different finite element models offers the engineer an additional way of performing verification. In this case, for example, both solid and axisymmetric models should produce identical answers provided the engineer had correctly modelled the problem and provided the FE software is sound for both model types; it is unlikely, although still possible, that a software issue extends to two different finite element models of the same problem.
Figure 5: Finite element models for the disc

### Finite Element Elastic Solution

The main stresses occurring in the disc are radial and hoop and, from theory, it is known that these vary in a quadratic manner with radius. The other stress components, axial stress and in-plane shear, will be small in comparison and can be safely ignored at least for a parallel sided disc. The variation in the radial and hoop stresses in the axial direction will also be small as the difference in the stresses for plane stress and plane strain is, from theory, small. As such it might be sensible to adopt a mesh refinement strategy that favours the radial direction over the axial direction. However, for the purposes of this challenge a uniform mesh refinement strategy will be adopted. Commercial FE systems generally offer a range of elements for axisymmetric problems. For this problem, the lower-order, four-noded element is used with reduced (single point) integration. The convergence of the hoop stress at the two ends of the centre line of the disc and at the centroid of the disc generator plane is shown in Figure 6.


Two commercial FE systems, CS1 and CS2, were used to produce the results in this figure. The element used was the four-noded quadrilateral with reduced integration. Although the elements appear, on the surface, to be identical, the element for CS1 adopts some form of selective integration and this leads to an underprediction of the stress by a factor of 3/4 for the single element. With mesh refinement both CS1 and CS2 converge to more or less the same result. For CS2 the hoop stress for the single element is exactly equal to the theoretical average hoop stress.

Figure 6: Solution verification for FE elastic hoop stress in the parallel disc (=1000rad/sec)

The elastic limit speed from the FE solution can be calculated in the same manner as the theoretical value and as the finite element hoop stress is practically identical to that from theory the elastic limit speeds are also virtually identical.

For the four-noded elements with reduced integration used in this challenge, the average hoop stress can be simply determined as illustrated in Figure 7 for a two-element mesh.


Figure 7: Calculation of the average hoop stress from a finite element model

It is interesting to note that the average finite element hoop stress is exactly equal to the average value from theory. This is the case for any mesh of elements even if they are distorted and is a property of the finite element method provided that a proper integration scheme is adopted – this is not the case for CS1 which uses a selective reduced integration scheme.

Thus, for the parallel sided disc and assuming an elastic-perfectly plastic material model that obeys the Tresca yield criterion, it is possible to predict the plastic limit load from an elastic analysis of a single finite element model using CS2.

### Finite Element Plastic Solution

A plastic finite element analysis can be conducted by considering an elastic, perfectly plastic material model together with an appropriate yield criterion. The theoretical plastic solution presented earlier adopted the Tresca yield criterion but this is not available in most commercial FE systems probably because its polygonal form gives multi-valued normal directions to the curve at the vertices. Most commercial systems do however offer the von Mises criterion which is elliptical in form and does not suffer from this problem. It should be noted also that in practice, the von Mises criterion is more appropriate (better represents) the yield of ductile metals as considered here, [5].

The finite element analysis applies the load incrementally until no more load can be sustained by the disc and this is then deemed the plastic collapse load. As with the elastic analysis, the disc was run through both commercial FE systems and the results are shown in Figure 8.

Unsafe FE Approximation!!

An elastic-perfectly plastic material model was used together with the von Mises yield criterion and a yield stress of 1000MPa. The result from CS1 unsafely overpredicts the plastic limit speed for the coarse meshes, c.f., the 3/4 factor mentioned in Figure 6. With mesh refinement both CS1 and CS2 converge to more or less the same plastic limit speed. The single element result for CS2 is identical to the theoretical plastic limit speed and the reason for why mesh refinement leads to a greater limit speed will be discussed further.
Figure 8: Solution verification of the plastic limit speed for the parallel disc

The plastic limit speed predicted by the finite element analysis (6460rad/sec) is about 4% greater than the theoretical value (6202rad/sec). The main reason for this is due to the different yield criterion adopted as shown in Figure 9.

The region of interest is the quadrant of the diagram where both principal stresses are positive. Both yield criteria have identical values where the principal stresses are equal and where the radial stress is zero. These correspond, respectively, to points at the centre of the disc and points on the periphery. At intermediate radii, the stresses may now increase beyond the line defined by Tresca to the curve defined by von Mises and the increase in speed is as identified above. As in the case of the theoretical plastic solution which showed, for Tresca, yield over the full disc, the same is true for the finite element model and the von Mises criterion. However, a difference is noted in the stress fields since whereas for the Tresca criterion the hoop stress was equal to the yield stress across the full disc, the hoop stress with the von Mises criterion can now increase beyond the yield stress to a maximum of about 1.15 times the yield stress as indicated in the figure.


The nodal principal stresses from a 16x16 element mesh are normalised with the yield stress (1000MPa) and plotted as points on the diagram. The polygonal yield criterion of Tresca is shown in blue and the elliptical von Mises criterion in black. The radial stress does not exceed the yield stress (1000MPa) but the hoop stress is able to exceed this by about 15% and this corresponds to the increase allowed when adopting the von Mises yield criterion over the Tresca criterion.
Figure 9: Normalised principal stresses for the parallel disc

In writing this response it was discovered that in CS2 the Tresca yield criterion could be simulated using the Mohr-Coulomb criterion with the friction and dilation angles set to zero and the cohesion yield stress set to half the material yield stress. This yield criterion is non-associative leading to a non-symmetric stiffness matrix and the requirement for an appropriate solver. However, the results produced provide a plastic limit speed identical to the theoretical solution presented earlier in this response.

### Tapered Challenge Disc

The challenge included, in addition to the parallel sided disc, a tapered disc for consideration. It is likely that as the taper in the disc increases the solution will begin to differ from that for the parallel sided disc and this is the case as shown in Figure 10 which presents the results of a parametric study where the taper of the disc is increased by increasing the central axial thickness for a fixed axial thickness at the disc periphery.


Figure 10: Burst speed as a function of disc taper (Theory and FE)

For the parallel sided disc the results already quoted are observed with the burst speed from FE being about 4% greater than that predicted by theory. The average hoop stress used in the theoretical result can be obtained either from a static analysis as shown in Figure 2, or by using a single finite element and the approach shown in Figure 7. As the ratio of the inner to outer axial thickness reaches about four the FE result crosses the theoretical value so that the theoretical prediction of burst now becomes non-conservative or unsafe. It should be noted that had the Tresca yield criterion been available for the FE result then the FE curve would have only been safe for the parallel sided disc where the two results would have been equal.

### Discussion

This challenge asked the reader to determine the burst speed of two discs, one parallel sided and the other tapered and an empirically derived method based on relating the average hoop stress determined from an elastic analysis to the ultimate strength of the disc material was provided. Theoretical expressions were developed for the average hoop stress in a parallel sided disc and it was shown that if the material is assumed to be perfectly plastic and to obey the Tresca yield criterion then the plastic limit speed can be obtained by simply equating the average hoop stress to the yield or UTS stress.

Finite element models were then prepared and it was seen that different commercial FE systems could produce different results for what, on the surface might be seen as the same element type. Further exploration showed that this was due to different integration schemes used in the codes and provided sufficient mesh refinement was undertaken then both systems converged to the same result. For CS2, which used a pure form of numerical integration, it was observed, irrespective of the mesh refinement or mesh distortion, that the finite element model recovered the exact value for the average hoop stress. Finite element analyses were conducted using an elastic-perfectly plastic material model together with the von Mises yield criterion. The elliptical yield criterion of von Mises allows the hoop stress to develop beyond the yield stress by about 15% and this leads to an increase in the predicted burst speed of about 4% over the Tresca criterion.

The tapered disc was then considered and it was seen that the empirical relationship presented in the challenge broke down soon after the disc moved away from the parallel sided geometric form.

In this study the influence of strain hardening has not been considered and, indeed, it has been tacitly assumed that the yield stress is equal to the UTS specified in the challenge. This may or may not seem a reasonable substitution since the actual stress/strain path is not being accurately followed. It is certain, however, that if this substitution is to be made safely, then the strain seen in the plastic analysis should not exceed that corresponding to the UTS. This has been checked for the parallel sided disc and, as can be seen in Figure 11, the total strain just prior to collapse is only about 2% which should be less than that at the UTS for the sort of materials from which discs might be manufactured.


The total strain at the point of peak strain is plotted against rotational speed. The strain plotted is the equivalent strain (von Mises) at the centre of the disc. It is seen that just prior to the plastic limit speed the strain is only about 2%.
Figure 11: Total peak strain as a function of speed for the parallel sided disc

Whether or not this substitution of the yield stress is appropriate though is questionable and there is some evidence that this approach might be inappropriate with the experimental results reported in a 1948 technical note to the National Advisory Committee for Aerodynamics, [6], – see Figure 12.


This figure effectively plots measured burst speeds of parallel sided discs, normalised (divided) by the speed to cause the first stress to exceed the UTS, against a measure of material ductility. Only one beryllium-copper disc reaches the speed predicted by the Robinson criterion! The red lines have been added to the figure and are based on an estimate of the yield stress being 0.8 times the UTS. The work undertaken by NACA can be considered as a validation exercise between a postulated theory or mathematical model (Robinson’s) and measured results. In this sense, validation can be seen to have failed and so either the mathematical model is incorrect or the measured results are not sound. Assuming the measured results to be sound then the mathematic model attracts suspicion. Since, for parallel sided discs as considered in this figure, the theory is correct, then it can really only be the material properties that are not applicable – use yield stress rather than UTS and all becomes clear!
Figure 12: Measured results from NACA burst experiments

As presented, the results of Figure 12 show the Robinson burst criterion to be rather inadequate even for parallel sided discs with discs failing prior to the mean hoop stress reaching the material UTS. A more satisfying picture is obtained if the yield rather than the ultimate stress is adopted as indicated by the red lines in the figure. In this case, with the exception of a single out-rider, all results are greater than the prediction and could be reasonably attributed, without further ado, to the strain hardening characteristics of the material.

Thus, in terms of the engineering design of rotating discs, this challenge has highlighted the potential limitations in adopting the empirical burst criterion of Robinson. For a disc exhibiting any reasonable taper the limiting speed would have been reached way before the average hoop stress had reached the yield stress! This observation has been made by others and for differently shaped discs and it provides a nice example of a situation where extending an idea beyond its theoretical limitations is fraught with danger. The work reported by Robinson and NACA does, of course, predate any possibility of the numerical modelling, through for example FE analysis, of such problems. Although the work of Weiss and Prager makes pretty clear the sort of considerations necessary. Thus, the reader might be surprised to learn that even today the Robinson design criterion plays a part in modern turbomachinery design. In reference [7], the Robinson design criterion can be found being used for the design of the discs of centrifugal compressors which are about as far removed from the parallel sided disc at it is possible to get! This example highlights the danger of the propagation of folklore; the thoughtful engineer needs to understand from whence these ideas come and assure him/herself of their applicability for the design being studied.

### Acknowledgements

The author would like to thank Ian Symington, Technical Officer at NAFEMS, and Alan Prior and his colleagues at Simulia for assisting the him with some of the technical hurdles involved in the plastic analysis of the rotating discs considered in this challenge.

### References

[1] Robinson, E., Bursting Tests of Steam-Turbine Disk Wheels, Trans. ASME 66, page 373, 1944.
[2] Stefano Chianese, Safety Factor Against Burst Speed of Turbomachinery Rotating Disks, MSc Thesis, University of Illinois, Chicago, 2013.

http://indigo.uic.edu/handle/10027/10185

[3], Hearn, E.J., Mechanics of Materials, Volume II, 3rd Edition, Butterworth-Heinemann, 2000.

[4] Weiss, H.J., & Prager, W., The Bursting Speed of a Rotating Plastic Disc, Office of Naval Research, Technical Report Number 96, September, 1953.

http://www.dtic.mil/dtic/tr/fulltext/u2/016990.pdf

[5] Taylor, G.I., Quinney, H., The Plastic Distortion of Metals, Philosophical Transactions of the Royal Society of London, Series A, Vol. 230, pp. 323-362, 1932.

www.jstor.org/stable/91233

[6] Holms, A.G., & Jenkins, J.E., Effect of Strength and Ductility on the Burst Characteristics of Rotating Discs, Technical Note 1667, National Advisory Committee for Aeronautics, Cleveland, Ohio, July 1948.

https://ntrs.nasa.gov/archive/nasa/casi.ntrs.nasa.gov/19930082292.pdf

[7] Robinson, C., Casey, M. and Woods I., An Integrated Approach to the Aero-Mechanical Optimisation of Turbo-Compressors, in Current Trends in Design and Computation of Turbomachinery, 2011.

http://www.pcaeng.co.uk/library/Publications/WhitePapers/turbostroje-2011_PCA-ENG.pdf

### NAFEMS PSE Competencies Identifier

ID | Competency Statement
FEAkn8 | List the requirements for an axisymmetric analysis to be valid.
FEAkn11 | Sketch problems showing the various form of symmetry.
FEAkn12 | List the advantages of using symmetry.
FEAco17 | Explain the process of Gaussian Quadrature and the terms Reduced Integration, Shear Locking and Mechanisms.
FEAco31 | Explain why most finite elements do not represent a circular boundary exactly …
FEAco35 | Discuss the terms Validation and Verification and highlight their importance.
FEAap3 | Illustrate the approximate nature of finite element analysis, through examples chosen from your industry sector.
FEAap14 | Carry out sensitivity studies.
MESMco3 | Explain the significance of the terms Equilibrium, Compatibility and Constitutive Relations.
MESMco14 | Provide examples of Plane Stress and Plane Strain.
MESMco15 | Explain the Tresca and von Mises Failure Criteria in 2D, sketching the failure surface.
MESMco16 | Discuss the stress states that give rise to maximum differences between the Tresca and von Mises criteria.
MASco11 | Discuss the terms elastic-perfectly plastic, kinematic hardening, isotropic hardening, Bauschinger effect, hysteresis loop.
NGECco4 | Outline how large displacements, plasticity and instability can interact in a collapse scenario.
NGECap2 | Conduct large displacement analyses.
PLASco4 | Explain the terms Limit Load and Plastic Collapse Load and explain why the latter is often a misnomer.
PLASco5 | Explain the terms First Yield Load, Ultimate Load and Plastic Instability Load.
PLASap2 | Use FEA to determine Limit Loads for a range of components.
PLASap3 | Use FEA to determine Plastic Collapse Loads for a range of components.
SIMMkn6 | V&V - State simulation V&V principles.
SIMMco7 | V&V - Explain the term solution verification.
SIMMco8 | V&V - Explain the term code verification.

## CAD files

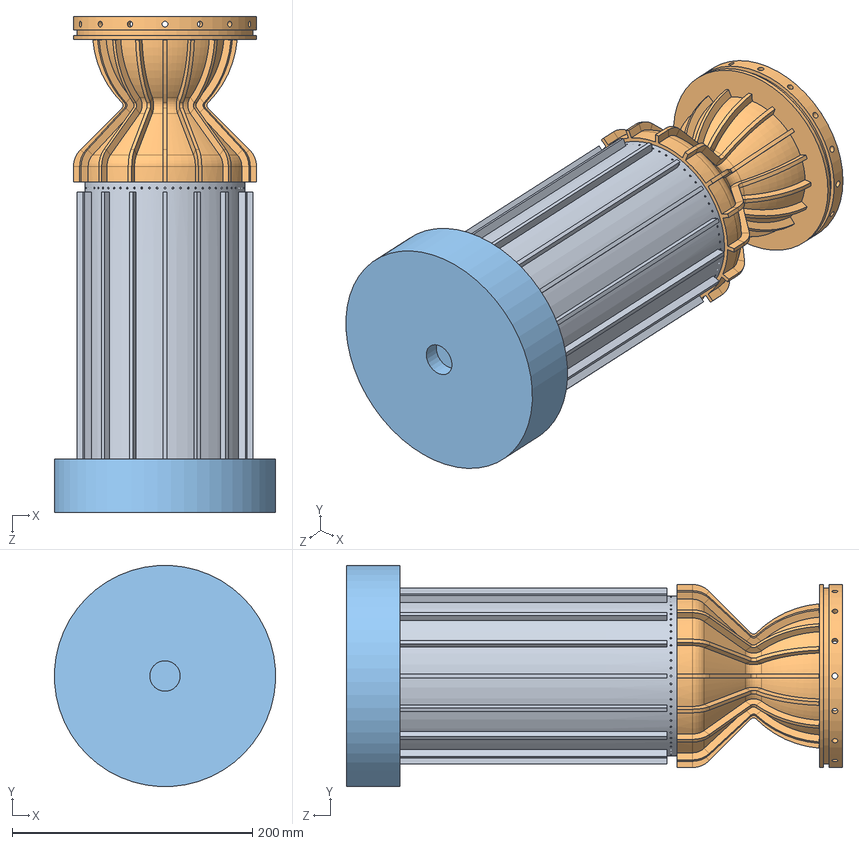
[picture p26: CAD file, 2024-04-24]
Solidworks Model/Combustion Chamber [CC]/[CC] Combustion Chamber.SLDASM
183.9 x 183.9 x 412.8 mm
[CC] Inner Chamber Wall
[CC] Inner Nozzle Wall
[CC] Injector Core

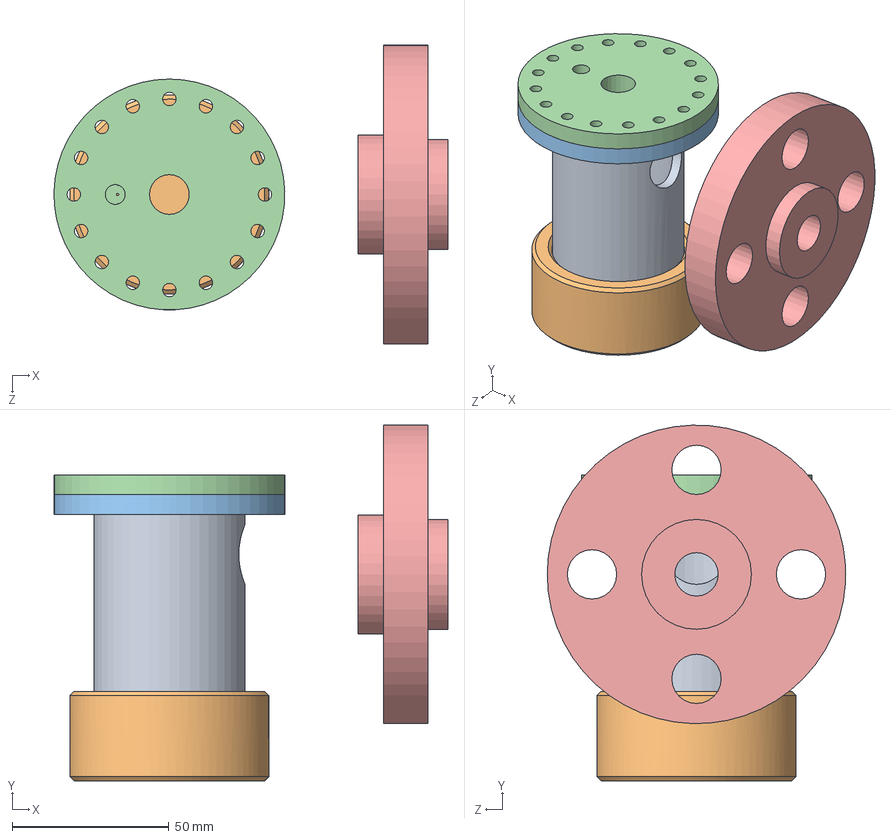
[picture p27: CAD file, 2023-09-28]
Solidworks Model/Gas Generator [GG]/[GG] Gas Generator.SLDASM
125.7 x 113.5 x 95.2 mm
[GG] Chamber
[GG] Chamber Bottom
[GG] Chamber Flange
[GG] Injector
[GG] Outlet Pipe Flange

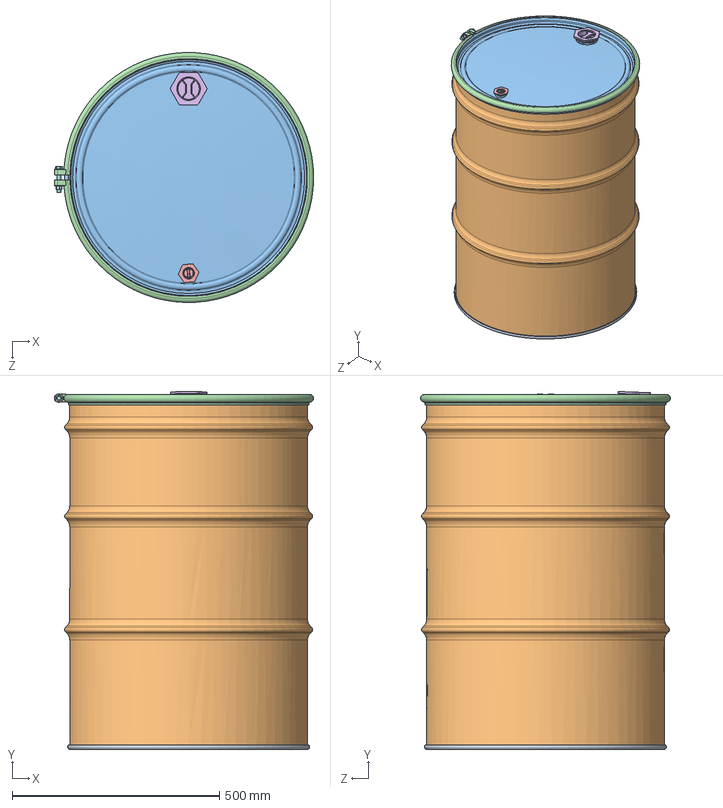
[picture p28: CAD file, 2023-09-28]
Solidworks Model/55GallonDrum.SLDASM
625.4 x 863.6 x 602.7 mm
Bottom
Lid
Clamp
_.75''pipePlug
_2''pipePlug
FW.38SAE x 2
HHCS.38-16x2.25ZpGr5t
HN.38-16

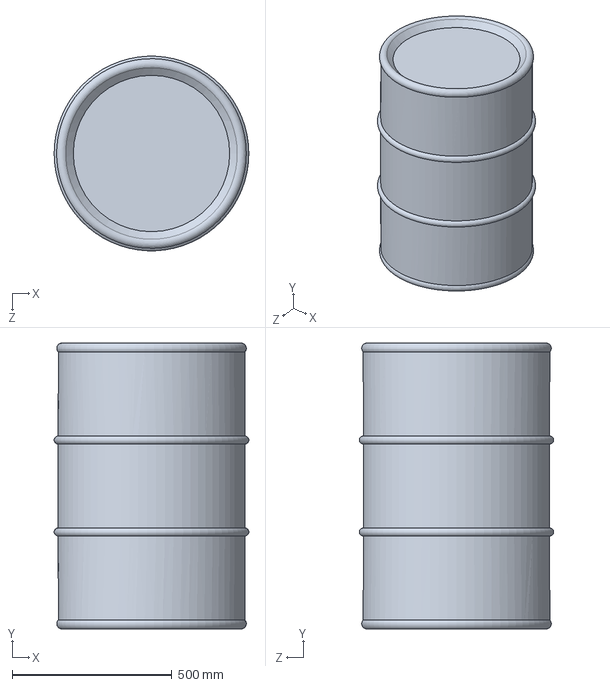
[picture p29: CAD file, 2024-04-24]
Solidworks Model/Feed System [FS]/[FS] Fuel Tank.SLDASM
609.6 x 895.3 x 608.9 mm

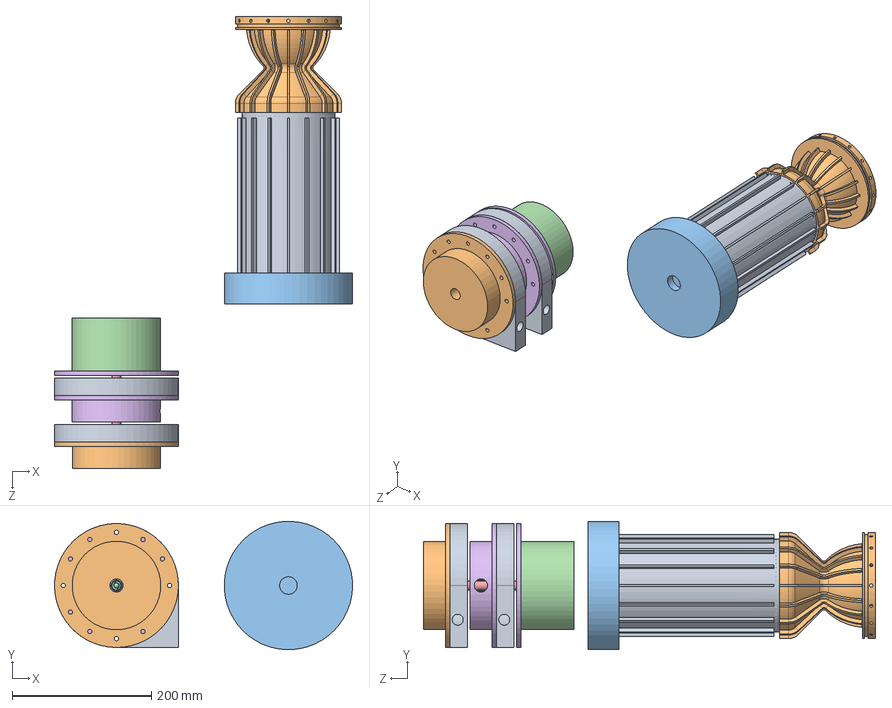
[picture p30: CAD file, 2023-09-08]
Solidworks Model/Full Engine.SLDASM
427.6 x 183.9 x 648.8 mm
[CC] Inner Chamber Wall
[CC] Inner Nozzle Wall
[CC] Injector Core
[TP] Turbine Housing
[TP] Diaphragm
[TP] Diaphragm Lid
[TP] Stator
[TP] Rotor
[TP] Pump Casing Volute x 2
[TP] LOx Pump Casing Cap
[TP] Impeller x 2
[TP] Inducer
[TP] Rotary Shaft
[TP] Fuel Pump Casing Cap

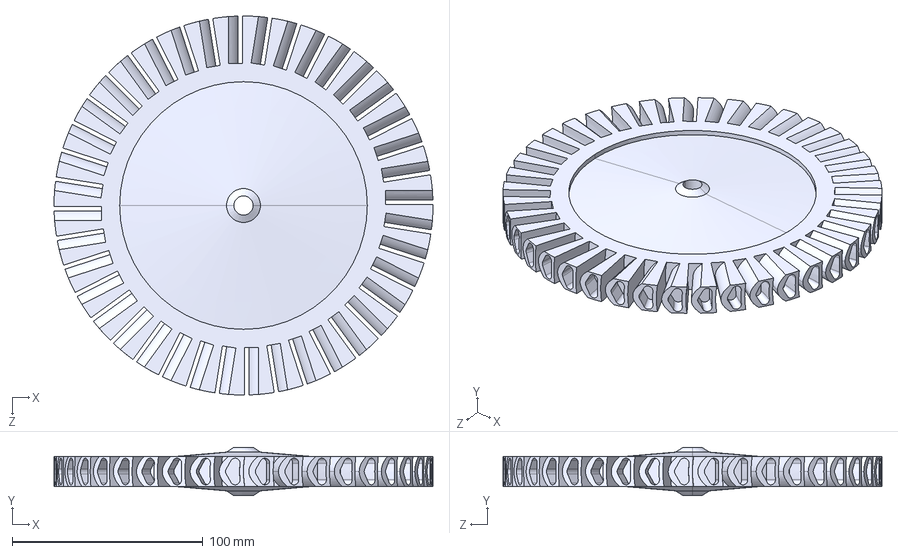
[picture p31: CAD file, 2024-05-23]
Ansys Models/Rotor/[TP] [Turb] Rotor55.STEP
198.7 x 25.4 x 198.7 mm

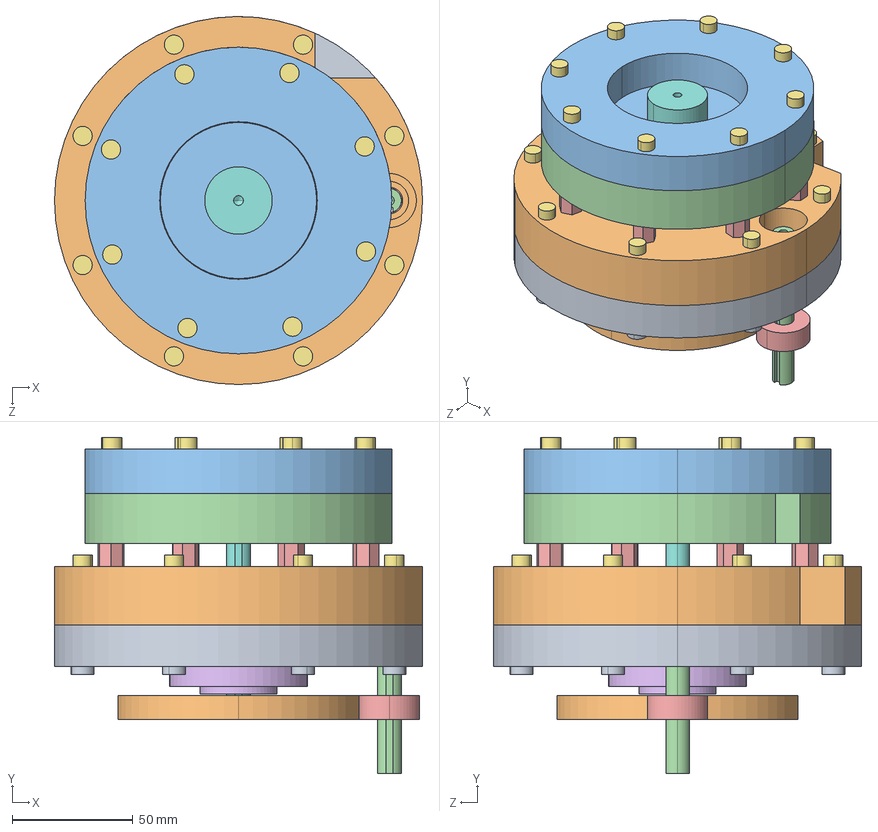
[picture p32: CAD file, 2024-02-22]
Ansys Models/Simplified CAD/Turbopump FEM 2.STEP
152.4 x 139.2 x 152.4 mm
[TP] [Pump] [Fuel] Pump Casing Cap_Simplified FEM
[TP] [Pump] [Fuel] Pump Casing Volute_Simplified FEM
[TP] [Pump] [Ox] Pump Casing Cap
[TP] [Pump] [Ox] Pump Casing Volute_Simplified FEM
Interpump Standoff FEM_91075A171 x 8
[TP] [Pump] [Fuel] Seal Retaining Cap
10-32-1.75 Fastener FEM x 16
[TP] [Pump] Keyed Shaft - 7398K211_304_7398K211
10-32 Nut FEM x 8
Pump Gear FEM
[TP] [Pump] [Ox] Impeller_Simplified FEM
[TP] [Turb] Keyed Shaft - 7398K211_304_7398K211
Turbine Gear FEM
[TP] [Pump] [Fuel] Impeller_Simplified FEM
[TP] [Pump] [Fuel] Inducer_Simplified FEM
[TP] [Pump] [Ox] Inducer_Simplified FEM

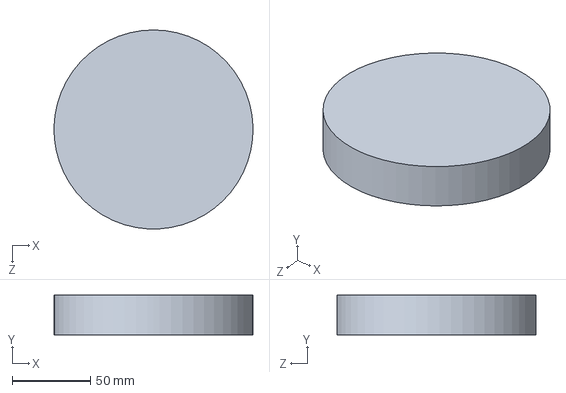
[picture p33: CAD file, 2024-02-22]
Solidworks Model/CAM/5 Inch Disc Stock.SLDPRT
126.9 x 25.4 x 127.0 mm

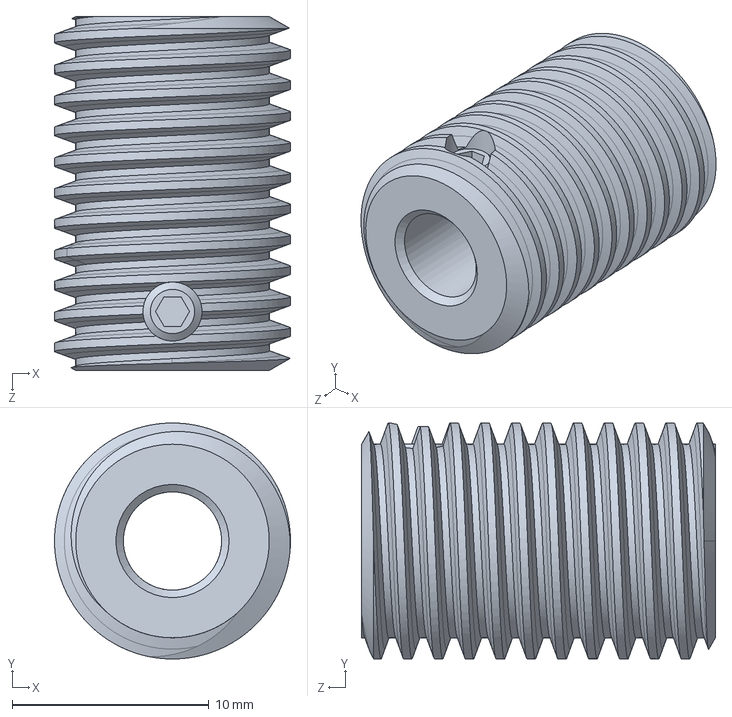
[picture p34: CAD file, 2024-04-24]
Solidworks Model/Feed System [FS]/[FS] 0.5 Module Worm.SLDPRT
12.0 x 12.0 x 18.0 mm

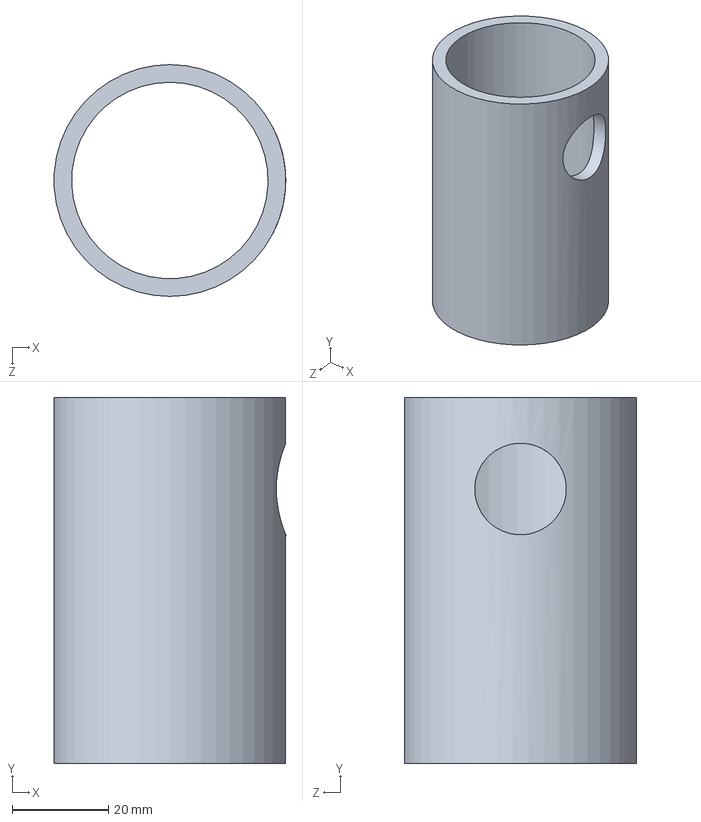
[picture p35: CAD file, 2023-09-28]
Solidworks Model/Gas Generator [GG]/[GG] Chamber.SLDPRT
48.2 x 76.2 x 48.3 mm

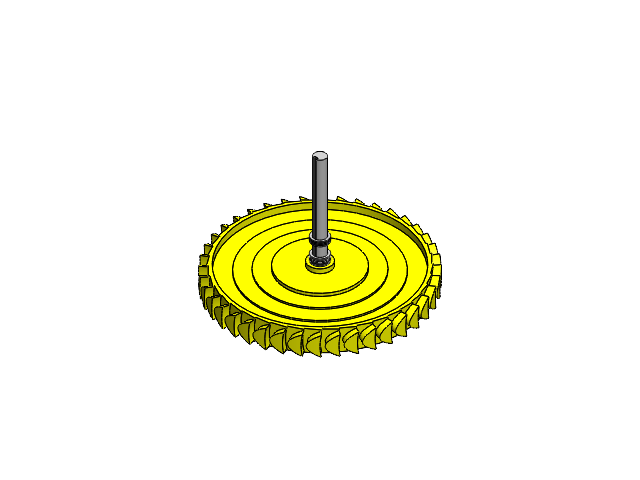
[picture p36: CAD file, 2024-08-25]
Solidworks Model/Turbopump [TP]/[Turb] Turbine/[TP] [Turb] Turbine.SLDASM
[TP] [Turb] Keyed Shaft - 7398K211_304
[TP] [Turb] Key
[TP] [Turb] Blisk
[TP] Shaft Spacer x 10

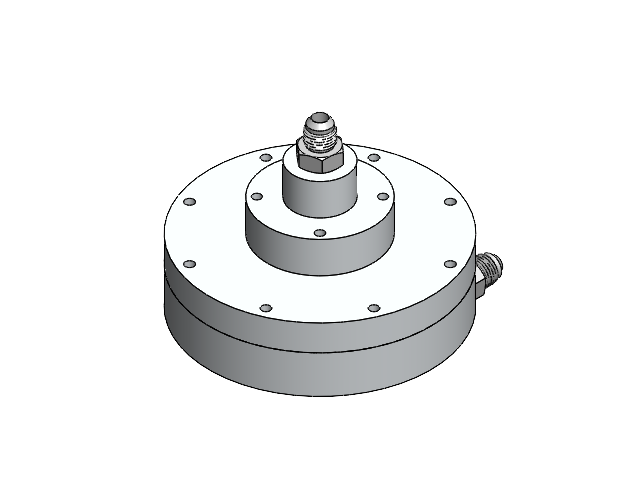
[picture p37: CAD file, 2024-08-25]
Solidworks Model/Turbopump [TP]/[Pump] Combined Pump/[Ox] Liquid Oxygen Pump/[TP] [Pump] [Ox] Pump.SLDASM
[TP] [Pump] [Ox] Pump Casing Volute
[TP] [Pump] [Ox] Pump Casing Cap
[TP] [Pump] [Ox] Impeller
[TP] [Pump] [Ox] Inducer
[TP] [Pump] [Ox] Inlet Cap
[TP] [Pump] [Ox] Inducer Retaining Bolt - 97763A342
[TP] [Pump] [Ox] PTFE O-Ring - 9559K224
[TP] [Pump] [Ox] Inlet Fitting - 50715K164_37
[TP] [Pump] [Ox] Small PTFE O-Ring - 9559K45
[TP] Flared Fitting - 50715K262

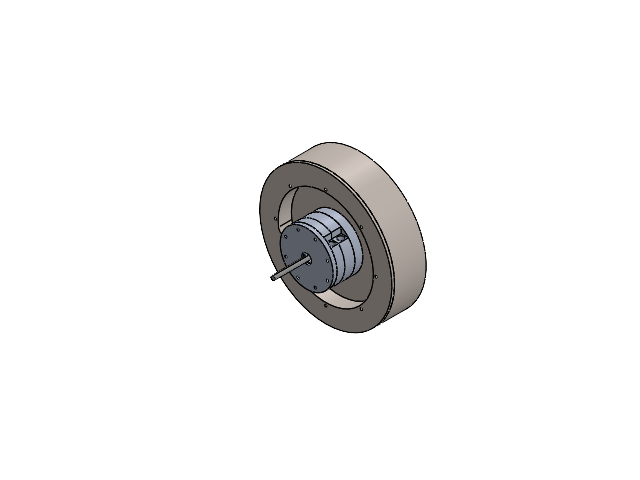
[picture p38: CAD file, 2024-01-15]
Solidworks Model/Turbopump [TP]/[TP] Turbopump.SLDASM
[TP] [Ox] Pump Casing Volute
[TP] [Ox] Impeller
[TP] [Ox] Pump Casing Cap
[TP] [Fuel] Pump Casing Volute
[TP] [Fuel] Pump Casing Cap
[TP] [Fuel] Impeller
[TP] Ball Bearing - 6138K14
[TP] [Fuel] Shaft Washer - 98017A253_18-8
[TP] [Turb] Manifold
[TP] [Turb] Outer Cover
[TP] [Turb] Nozzle Plate
[TP] [Turb] Rotor - Stage 1
[TP] [Turb] Sandwich Plate
[TP] [Turb] Stator
[TP] [Turb] Rotor - Stage 2
[TP] Main Shaft - 7405K2_316

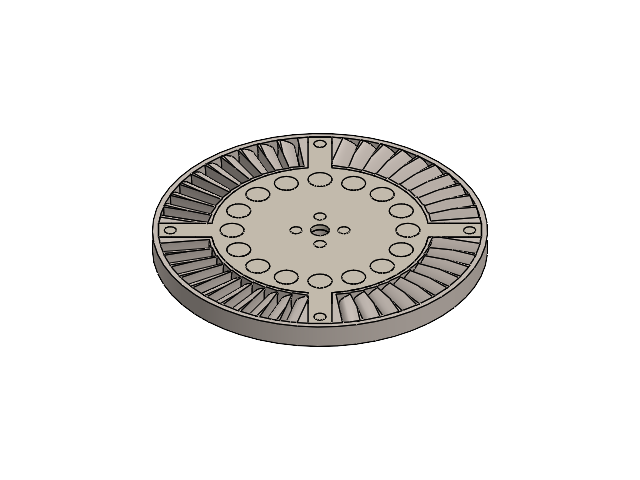
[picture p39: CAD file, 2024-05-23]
Solidworks Model/Turbopump [TP]/[Turb] Turbine/[TP] [Turb] Impulse Rotor.SLDASM
[TP] [Turb] Blisk
[TP] [Turb] Rotor Outer Plate x 2
[TP] [Turb] Blisk Column Pins x 16
[TP] [Turb] Rotor Blade Retaining Ring
[TP] [Turb] Small Column Pin x 8

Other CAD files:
Solidworks Model/Feed System [FS]/[FS] LOx Tank.SLDASM
Solidworks Model/Turbopump [TP]/[GG] Gas Generator/[TP] [GG] Gas Generator.SLDASM
Solidworks Model/Turbopump [TP]/[Pump] Combined Pump/[Fuel] Ethanol Pump/[TP] [Pump] [Fuel] Pump.SLDASM
Solidworks Model/Turbopump [TP]/[Turb] Turbine/[TP] [Turb] Rotor.SLDASM
Ansys Models/Rotor/[TP] [Turb] Rotor.STEP
Ansys Models/Rotor/[TP] [Turb] Rotor1.STEP
Ansys Models/Rotor/[TP] [Turb] Rotor10.STEP
Ansys Models/Rotor/[TP] [Turb] Rotor11.STEP
Ansys Models/Rotor/[TP] [Turb] Rotor12.STEP
Ansys Models/Rotor/[TP] [Turb] Rotor13.STEP
Ansys Models/Rotor/[TP] [Turb] Rotor14.STEP
Ansys Models/Rotor/[TP] [Turb] Rotor15.STEP
Ansys Models/Rotor/[TP] [Turb] Rotor16.STEP
Ansys Models/Rotor/[TP] [Turb] Rotor17.STEP
Ansys Models/Rotor/[TP] [Turb] Rotor18.STEP
Ansys Models/Rotor/[TP] [Turb] Rotor19.STEP
Ansys Models/Rotor/[TP] [Turb] Rotor2.STEP
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

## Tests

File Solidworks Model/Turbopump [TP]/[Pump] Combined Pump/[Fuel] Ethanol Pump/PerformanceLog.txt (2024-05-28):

Number of Contacts: 24
Number of contact data: 2228

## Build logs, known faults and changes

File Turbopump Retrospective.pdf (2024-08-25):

# Turbopump Retrospective

Brendan Morgan

# Contents

## Summary

3

## I. Design

4

## Goals

4

## Overall Layout

4

## Impeller Geometry

6

## Profile Curve

7

## Blade Curve

8
Inducer Geometry | 10
Volute Geometry | 12
Turbine | 15
Rotor Blade Geometry | 16
Rotor Blisk Geometry | 17
II. Manufacturing Process | 18
Impellers/Inducers | 18
Pump Casings | 18
Rotor | 20
Shafts | 21
Turbine Housing | 22
III. Testing | 24
First Spinflow Test (6/16/2024) | 25
Main Issues with First Test | 26
Second Spinflow Test (7/3/2024) | 28
Sourcing / Tools | 29
Helpful People | 29
References | 29

# Summary

I (Brendan Morgan) designed/analyzed/machined/welded/integrated one complete turbopump, with serious design work beginning in September 2023 and two tests occurring the nights of June 16 and July 7, 2024. I wrote this document for two purposes: one, for myself to remember in detail what I have done so I can expand and improve upon it in future versions; and two, for any others who are interested in doing something similar. I am far from any kind of expert in turbomachinery, but perhaps my approaches, both the successes and failures, might be helpful to someone starting from a similar point as I did to get started and avoid some pitfalls. This report is far from exhaustive. I’m mainly covering the most important design decisions, equations, and high level overviews of manufacturing processes.

I’m calling the tests a “spinflow” (turbine spin-up + pump waterflow). The turbine is spun up using pressurized nitrogen gas from bottles, and water flows though both pumps. The nitrogen gas is attempting to simulate a 0.557 kg/s (1017 SCFM) gas flow from a theoretical gas generator. The water is attempting to simulate a 4.5 kg/s flow of liquid oxygen and a 3.8 kg/s flow of 75% ethanol fuel. It is attempting to pressurize the oxidizer outlet to 428 psi and the fuel outlet to 448 psi.

Most design and analysis work can be found on my github and google drive (though many things are quite unpolished and unorganized). Also note there is quite a bit of code and design work on a regeneratively cooled combustion chamber, because the turbopump originally began as part of a larger project to do a full GG cycle. I intend to return to this someday, but for the purposes of this report these sections are not relevant and I won’t be referring to them again.

If anyone does want to do something similar, please take things in this report with a grain of salt, and check against other sources (a few are cited at the end). I am usually reachable on LinkedIn if anyone wants to discuss my experience further to help with their own project.

https://github.com/BrendanJMorgan/Engine-Development

https://drive.google.com/drive/u/0/folders/1xzCn_89ndQEU2PsFcl7RbZjL71s8Y_nX

# I. Design

# Goals

### - Supply sufficient fuel and oxidizer for a ~3000 lbf thrust engine - Target outlet pressures of 448 psi for fuel and 428 psi for ox - Drive pumps using gas turbine, not electric motor

- Optimize for manufacturability and integration. Did not prioritize optimizing for mass, if at all (that can come in later versions).

# Overall Layout

The turbopump has three major sections: an ox pump on the top, a fuel pump in the center, and a gas turbine at the bottom (ordering PPT). The two pumps are on one common shaft, and the turbine on a separate shaft. These two shafts are geared together so the turbine is significantly offset laterally from the pumps. This can all be seen in figure 1 on the following page.
The main alternative to this ordering would be to put the turbine in between the two pumps (ordering PTP). I went back and forth on this for a few weeks but settled on the PPT design because:
(1) The turbine could dump exhaust straight to atmosphere, without anything in the way. This eliminates the need for any kind of exit ducting, simplifying manufacturing.

### (2) It separates the coldest (ox pump) and hottest (turbine) sections as far apart as possible. This simplifies thermal management as opposed to the PTP design which would have an extreme thermal gradient between the turbine and both pumps

immediately adjacent to it.

### (3) Gearing would be much more difficult in a PTP design, as the rotor itself would very likely clash with the pump shaft. This would require either much larger gears to offset the rotor even further laterally, or more complex gearing to put it at an angle. The PPT

design allows the rotor to be harmlessly placed below the bottom of the pump shaft.

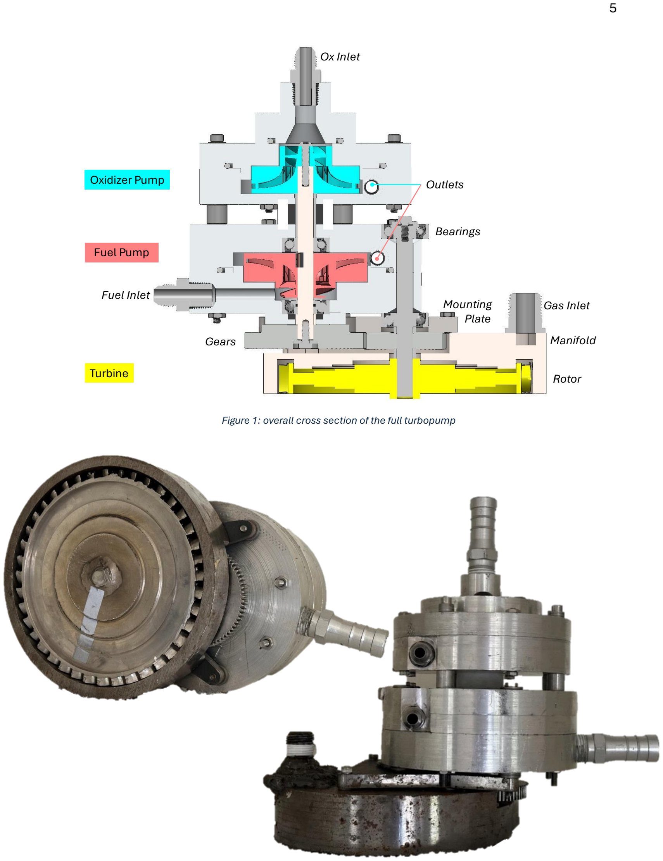
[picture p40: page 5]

Figure 1: overall cross section of the full turbopump

Turbine

Fuel Pump

O idi er Pump

ears | anifol as nlet

earings

otor

nlet

Fuel nlet

utlets

ounting
late

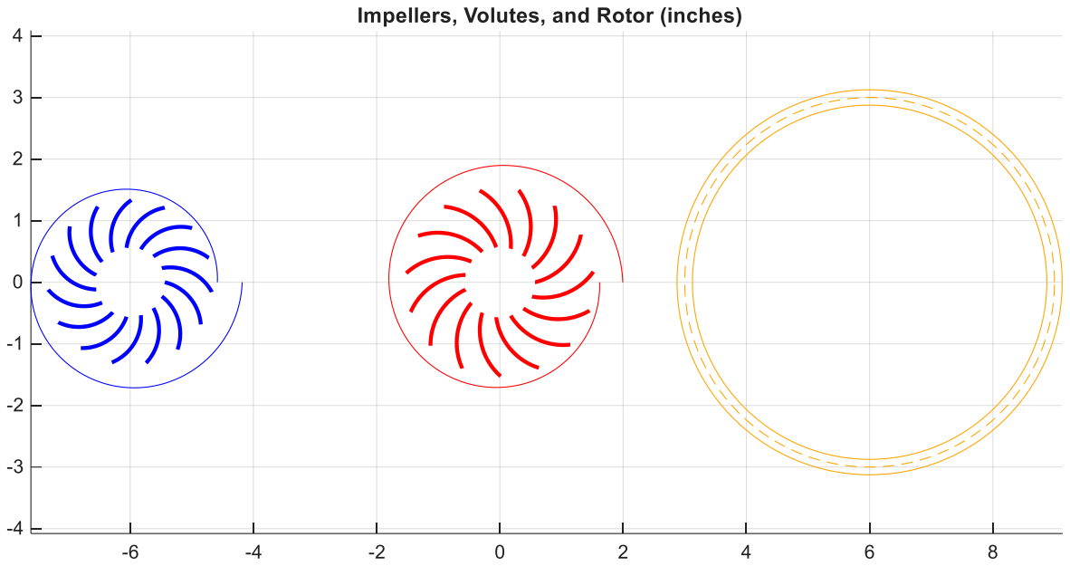
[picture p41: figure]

Figure 2: pump contours (left), fuel pump contours (center), turbine rotor contours (right). For scale comparison purposes; more etail given in following sections.

# Impeller Geometry

The impellers are a fully shrouded, centrifugal design with axial inlets that smoothly contour to radial outlets, with smoothly contoured blades that divide the flow into many internal channels. They are designed to rotate at 20,000 rpm; I settled on this value through trial and error in MATLAB. Faster yields an impeller too small and impractical to have 3D printed with decent channels to allow flow through, and faster tends to make the turbine impractical (either too large or needing too

### high of a gas flow)

The geometry of the contour between the inlet and outlet of the impellers, as well as the geometry of the blades and the volute, were primarily constructed using the pump handbook, especially pages 2.28 – 2.42 (Karassik, Messina, Cooper, & Heald, 2008).

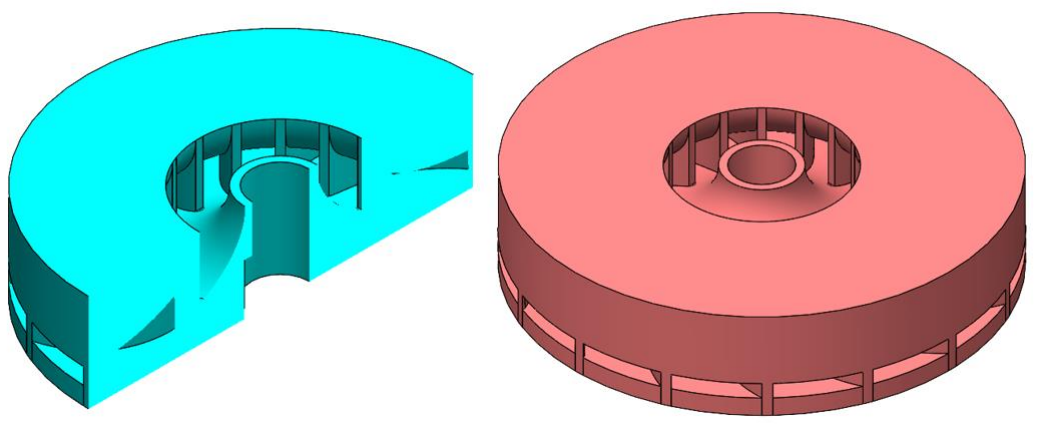
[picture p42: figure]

Figure 3: impeller (sectione ) an fuel impeller

Three parameters are established first to si e the impeller: the specific speed Ωs, the e it

flow coefficient φi, and the head coefficient Ψ. The following are the relationships from pump handbook I used to determine these; equations (2) and (3) are empirical and use SI base units. Q is the volumetric flow rate requirement of the pumped fluid, and ΔH is the head rise requirement (i.e. ΔH = Δp / g). Ω is the pump shaft speed; I chose a value of 20,000 rpm (2094 rad/s). This choice both to met the recommendation for specific speed to be between 0.1 and 0.6 for centrifugal pumps (0.36 and 0.29 for o and fuel) and outputted reasonable geometry at the end for the profile and blade curves, as well as a reasonably

machinable volute geometry.

Ωs =

Ω√Q
(gΔH)

3/4

(1)

ϕt = 0.1715√Ωs
(2)

ψ =

0.4

Ωs

1/4

(3)

## Profile Curve

To construct the profile of the impeller, two different curves are generated in MATLAB: first a shroud curve, and then an impeller curve derived from that. The two curves are shown in the figure below.

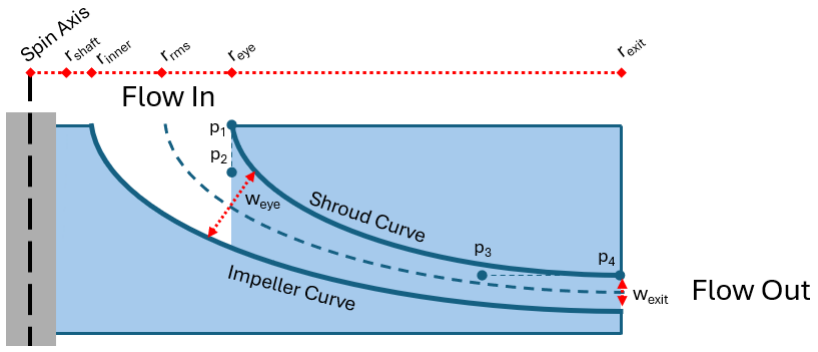
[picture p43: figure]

Figure 4: eneric impeller cross section. Flui flows a ially own into the top an ra ially out the right si e.0
There are three key parameters that mostly constrain the shape of the curves: the radius of the eye reye, the radius of the e it re it, and the width of the e it we it. The following three equations show how to calculate these parameters. Equation 1 is transcendental, so reye is found using a MATLAB solver. φe is the eye’s flow coefficient; a range of 0.2 – 0.3 is typical for impellers so I split the difference and assumed a value of 0.25.

reye =
[

Q
πΩϕe (1 −
rinner

2

reye

2 )
]

1/3

(4)

rexit =

1
Ω

√
gΔH
ψ

(5)

wexit =

Q

2πΩrexit

2 ϕϵ

(6)

Much more detail on all this can of course be found in pump handbook. The blockage parameter is calculated from the blade geometry, so for high accuracy the whole impeller + blades scripts are repeated until this converges. The following are some of the key values I settled on for my design, and the actual curve for both impellers.

| O Impeller (mm) | Fuel Impeller (mm)
rshaft | 5 | 5
rinner | 6.35 | 6.35
reye | 14.29 | 14.49
re it | 33.91 | 38.76
we it | 2.87 | 2.57

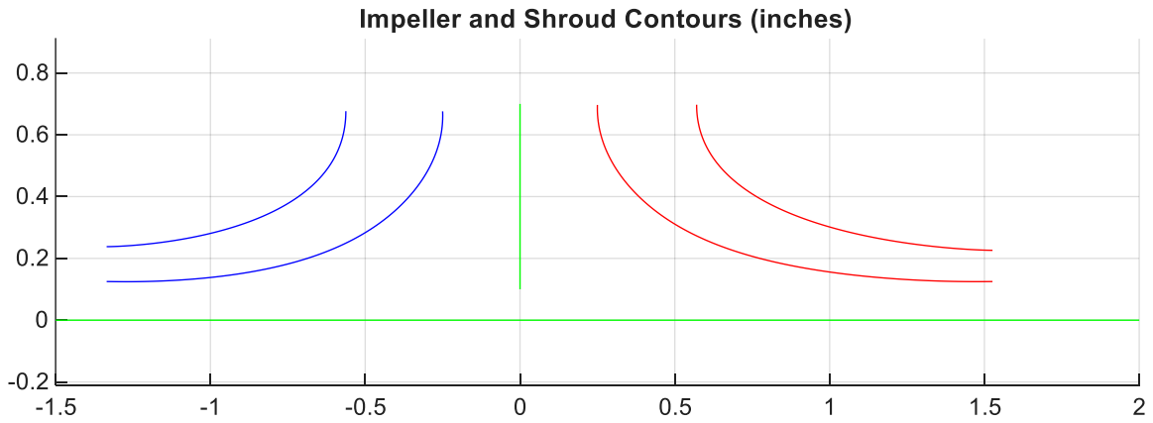
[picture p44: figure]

Figure 5: Cross sections of o impeller (left) an fuel impeller (right). The space between the curves is where flui flows.

## Blade Curve

The two main constraints on the shape of the blades are the inlet and outlet angles. Figure 6 below shows the geometry of one blade; the rest would be duplicates of this, rotationally symmetric about the pump’s spin a is.

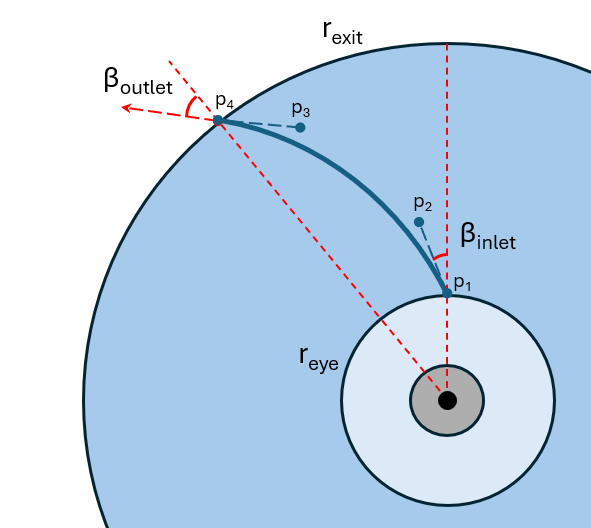
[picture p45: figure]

Figure 6: eneric impeller bla e profile. Flui flow ra ially outwar s.
The three equations below show how to find the inlet and outlet angles. ηHY is the combined hydraulic efficiency; equation 8 is Jekat’s formula, an empirical relationship (using SI base units) that accounts for all major sources of fluid inefficiency. μ is the slip factor; the

## Buseman relationship assumes it is between 0.1 and 0.2 so I split the difference and

assumed 0.15. One could do a good bit more calculation to get a more precise slip factor.

tan βinlet =

Uinlet

Vinlet

=

Ω⁄reye

Q⁄2πreyebeye

(7)

ηHY ≈ 1 −

0.071
Q⁰.25 | (8)

tan βoutlet =

Q/(2πrexitwexit)

Ωrexit(1 − μ) −

gΔH
ηHYΩrexit

(9)

### The fuel impeller’s blade inlet angle should be 76.4o

. In actuality because of a MATLAB coding error,

### the impeller was printed with a blade inlet angle of 88.1o

### . Similarly, the ox impeller should be at 76.5o but was made to 88.2o

### . Also, the ox impeller should have had 15 blades but did have 16. The

fuel impeller has 15 blades regardless. This may be a factor (but I suspect a rather minor one) in the low head achieved during the spinflow tests.

~
Once sufficiently constrained by the parameters, the actual curves that form the profile contours and the blade contours are all Bezier curves. They are constructed with four control points (I used the minimum possible number), where the inlet and outlet locations serve as a control point (points p1 and p4 in figure 4 & 6) and the other two are at some location along the flow vectors from these locations (points p2 and p3 in figure 4 & 6). The exact distances they are away are left as free parameters for a MATLAB solver, which attempts to minimize the entire curvature of the contour. According to pump handbook, the radius of curvature should ideally never go below half the eye radius to avoid excessive cavitation in the fluid.

The detailed calculations and numerical parameters for everything can be found in the MATLAB scripts impeller.m, and blades.m (themselves subfunctions of pump.m < powerhead.m < main.m) in the project github, linked in the summary section.

### The impeller geometry derivation may seem simple, but it probably took me the longest to

completely work out in MATLAB compared to all other aspects of the turbopump. Granted this may be because I did it first, but even so getting all the solvers to work correctly and work together is a task that should not be underestimated. Below are the key parameters I settled on for the blades. Actual plots for the blades can be found in figure 2 earlier.

# Inducer Geometry

## Both pumps have inducers to combat cavitation. Lo is assumed to be at 1 atm saturation when it enters the pump, so would immediately cavitate inside the impeller without an upstream inducer. The fuel is not so close to cavitation, but nevertheless still requires

some NPSH before it reaches the impeller.

Figure 7: n ucer (left) an fuel in ucer (right); sectione an unsectione mo els are the same.

## The o inducer is a shrouded, centrally hubbed design with a ial flow through its whole

length. Both it and the fuel inducer can be seen in figure 7.
The fuel inducer, while still centrally hubbed, is different in that it accepts inlet flow radially.

## Over half its length is unshrouded, while the bottom part (closest to its outlet and the

impeller) is shrouded. This radial inlet turned out to be a large mistake and is likely the primary reason for anemic flow in the fuel pump during the spinflow test. Essentially, it’s flow coefficient was likely very close to ero. I had designed it this way to make the design

## more compact and easier to integrate, but a future design should certainly accept flow

a ially.

## There are three main parameters that determine each inducer’s geometry. NPSHSE is net

positive suction head, shockless entry: i.e. how much head rise the inducer must induce in the fluid before it reaches the impeller so that it does not cavitate at the impeller entrance (hence “shockless”). The hub to tip ratio ν is a design choice; I used a value of 0.40 for both inducers. I applied an additional factor of 1.5 to the NPSH, as a safety margin.

NPSHSE = 1.2Φe

2 + [0.2334 + (

ωr
128.3

)

4
] (Φe
2 + 1) | (10)

SS is suction specific speed, a dimensionless parameter that serves as the inducer version of an impeller’s specific speed.

Ss =

nQ

1/2
NPSH³/4
| (11)

The optimal flow coefficient φoptimal quantifies the efficiency of the inducer at allowing fluid

## flow into through it’s entrance and is used in the calculation of an optimal inducer tip

radius rtip (that is, the ID of the shroud). The hub to tip ratio ν is a design choice; I used a value of 0.40 for both inducers.

Φoptimal =

1.3077√1 − ν
2/Ss

1 +

1
2

√1 + 10.261(1 − ν
2)/Ss

(12)

rtip = 1.449 [
Q
(1 − ν

2)ΩΦoptimal]

1/3
(13)

Blade lead Λ is the distance any individual blade advances per turn; it is a function of blade angle β. This angle is determined via the ratio α/β (flow incidence angle / blade angle); I used a value of 0.35. Lead is in turn used with solidity σ (I used a value of 2.5), to find the minimum required length of the inducer.

Λ = 2πr tan β | (14)

ℎmin =

Λσ
N
sin β | (15)

The following table lists parameters I settled and used for my actual design.

| O Inducer | Fuel Inducer
NPSH | 22.33 m | 9.00 m
Ss | 2.28 | 4.62
rtip | 13.4 mm | 16.5 mm
β | 24.8 deg | 14.2 deg
Λ | 39.0 mm | 26.3 mm
hmin | 10.2 mm | 4.0 mm

# Volute Geometry

Both pumps use a volute geometry to collect the fluid discharge from the impellers. This is commonly used over a vaned diffuser geometry; it is less sensitive to off design conditions

## and much easier for me to manufacture in a 3 a is CNC. Each pump casing has two halves

that seal together with PTFE O-rings. The volute profile is a spiral, which I intentionally had

## converge to a square right at the end of its path. This is to somewhat match the circular

outlet hole which ultimately transitions to an AN fitting. Shown here are the designs of the four machined pieces.

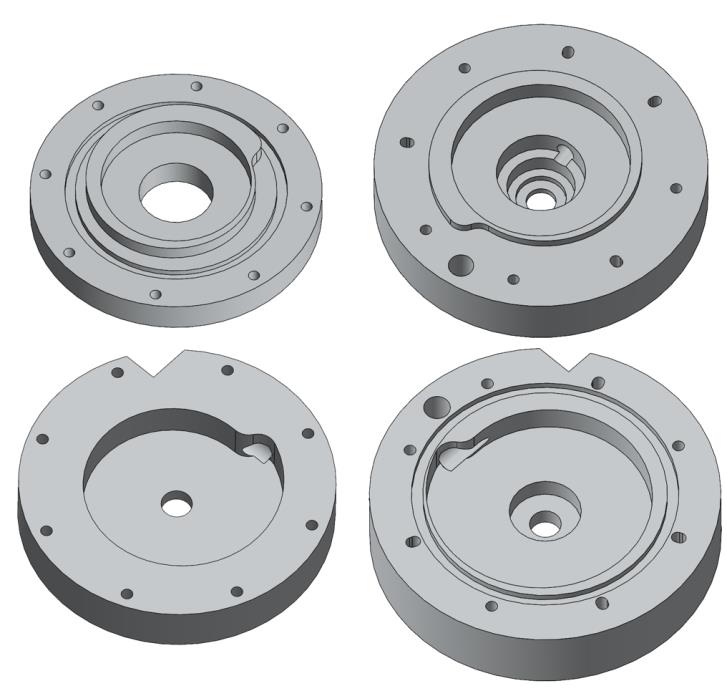
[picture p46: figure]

Figure 8: | volute (left) an fuel volute (right). The top row are the outboar halves an bottom row are the inboar
halves. | flow irection is counter-clockwise, fuel flow irection is clockwise.

## The following pictures show how these pieces fit together and with the rest of the turbopump assembly. The fuel casing also doubles as what is essentially the structural core of the whole turbopump – it is assembled first during integration, then the lo pump

mounted to its top, then the turbine manifold mounted below it with the rotor shaft passing

## through the outer material of the fuel pump casing. This casing actually holds all four bearings (two for pump shaft and two for turbine shaft); intentionally so because in real operation it would be the only part of the turbopump seeing reasonable temperatures that

would not destroy the ball bearings (i.e. free e or burn off their lubricant).

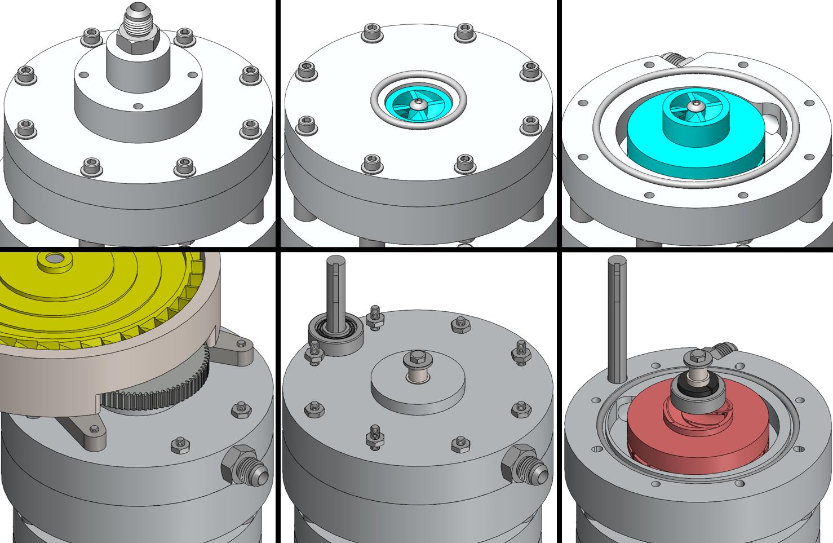
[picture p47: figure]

Figure 9: ump pieces in conte t of full turbopump assembly. on top, fuel on bottom.
The following ae the actual design values I used for the volute. Some of these values, especially the tongue thickness ttongue, were impractical to reali e to any great accuracy

## (because the tongue doesn’t have a uniform thickness since the outlet is circular) so the

value shown is just a target. The re it is the same as the impeller radii from earlier in the

## report. Further design guidance on this can be found in pump handbook (pg. 2.40-2.44) and

the MATLAB script volute.m.

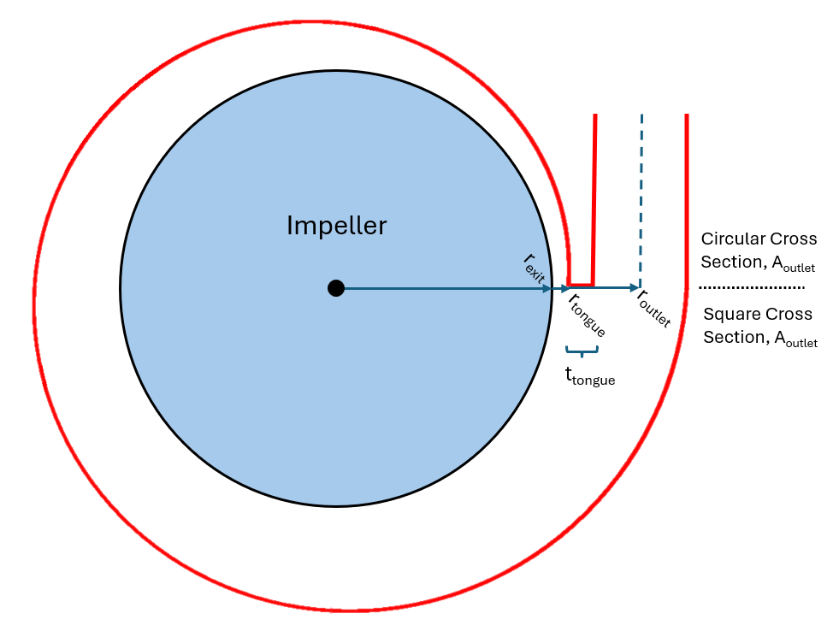
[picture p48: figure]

Figure 10: eneric volute profile. The manufacture volutes have a rectangular cross section until the e it, then circular.
| O Volute | Fuel Volute
re it | 33.9 mm | 38.8 mm
rtongue | 35.9 mm | 41.1 mm
ttongue (theoretically) | 0.9 mm | 1.1 mm
routlet | 41.5 mm | 46.4 mm
Aoutlet ( = hvolute 2 ) | 94.8 mm² | 81.0 mm²
hvolute | 9.3 mm | 84.7 mm

# Turbine

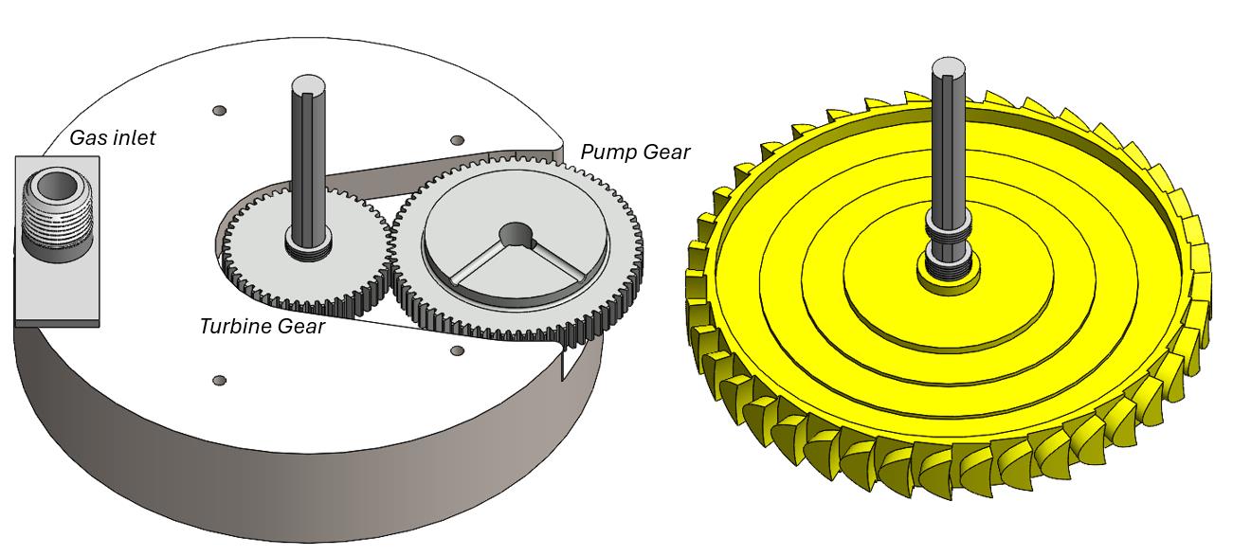
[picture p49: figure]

Figure 11: Turbine assembly, with manifol (left); an without, revealing the rotor (right)

## The turbine is an impulse design, with an unshrouded 304 stainless steel rotor placed

inside a carbon steel manifold. The turbine shaft is designed to spin at 30,000 rpm, so it is

## geared off at a 3:2 ratio from the pump shaft which is designed to spin at 20,000 rpm. I chose this turbine speed because it was the fastest that I could support with readily

available McMaster angular contact bearings. There is a tradeoff between turbine speed, its pitchline radius (i.e. the radius of the blades’ centerline), and the required gas flowrate. I

## was interested in minimi ing radius, to cut down machining time/comple ity and stick to more readily available stock on both the rotor and manifold; and in minimi ing gas flow

simply because nitrogen gas bottles can only supply so much during a spinflow test.

## Rotor Blade Geometry

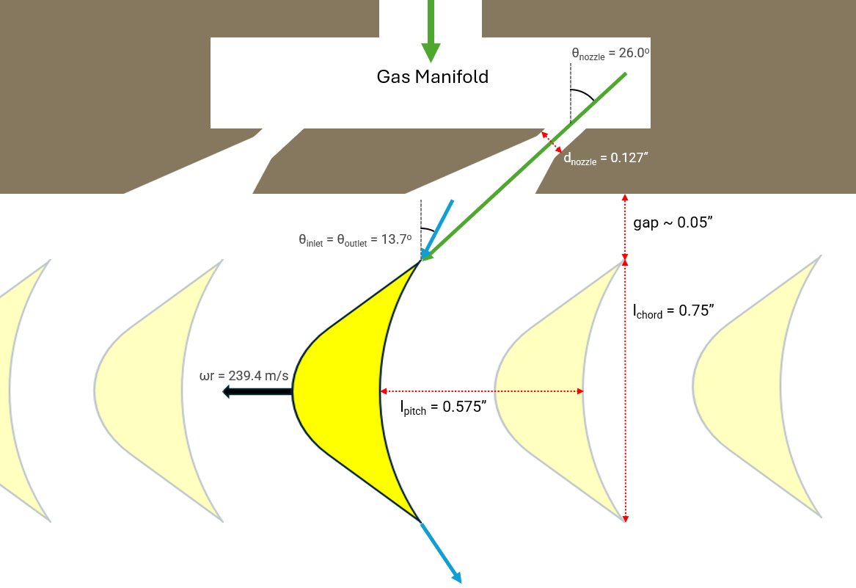
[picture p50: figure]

Figure 12: gas flowpath through rotor bla es. reen is flow in a stationary frame of reference while blue is flow in a corotatin frame of reference with the rotor.
The purpose of the blades is to redirect the incoming flow from the manifold no les, which imparts an impulse to the blades themselves and drives the rotor in a clockwise direction. The intention is that there is no post-swirl for ma imum efficiency; i.e., in a stationary frame of reference, the gas e its the rotor moving straight down, not diagonally. In the relative

## (corotating) frame of the blades this means the flow has the same incoming and outgoing

lateral speed, just in opposite directions. For this reason the incoming and outgong blade angles are identical, making the blades symmetric as shown in the above figure.

## A principal concern in designinig the turbine is knowing how much power it must acutally supply to meet the needs of the two pumps. For this a full efficiency needs to be calculated, which includes multiple inefficiency coefficients. Namely e pansion energy

loss (φ), which is a function of blade deflection angle; an empirical curve can be found in the NASA turbines paper cited at the end. The kinetic energy loss coefficient (Ψ), is also a direct function of φ. Ci is the incidence angle loss coefficient, and Cm is the mach-number

## coefficient; empirical data for both of which can be found in the NASA turbines paper as

well.

Δℎe = Δℎes + Δℎev = Δℎs

⋅ ϕ

2 + Δℎv ⋅ ψ

2
⋅ Ci
⋅ Cm | (16)

ψ

2 = 2φ

2 − 1 | (17)

## Rotor Blisk Geometry

The principal structural concern of the rotor is centrifugal stress – i.e. its burst speed. I quickly found that torque on the blades had negligible stresses comparatively, even if the blades were significantly longer.

The rotor has a stepped profile to survive the centrifugal stress. I.e., the amount of mass far from the axis is minimized while still being thick enough to support the ‘weight’ of the blades along the rim. A shrouded rotor is best from a fluid efficiency perspective, but I realized after many iterative attempts that this was untenable from a structural perspective – it adds too much mass very far from the central axis.

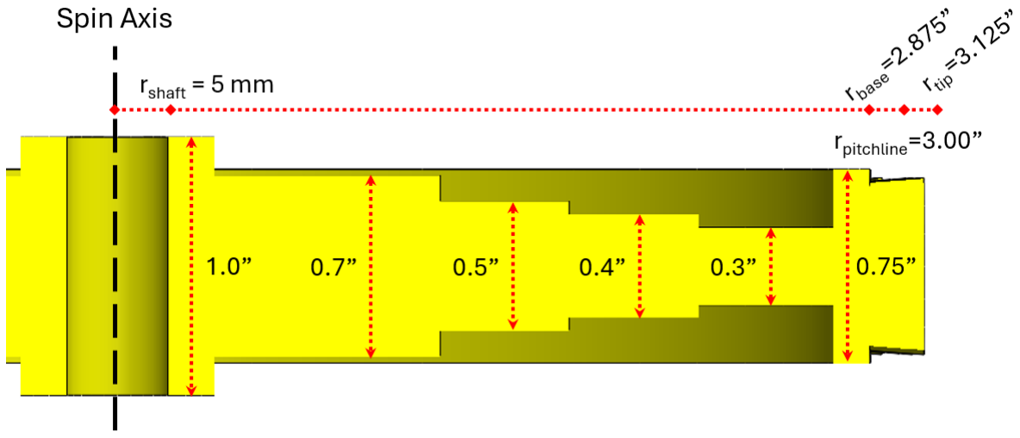
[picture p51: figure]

Figure 12: otor steppe profile

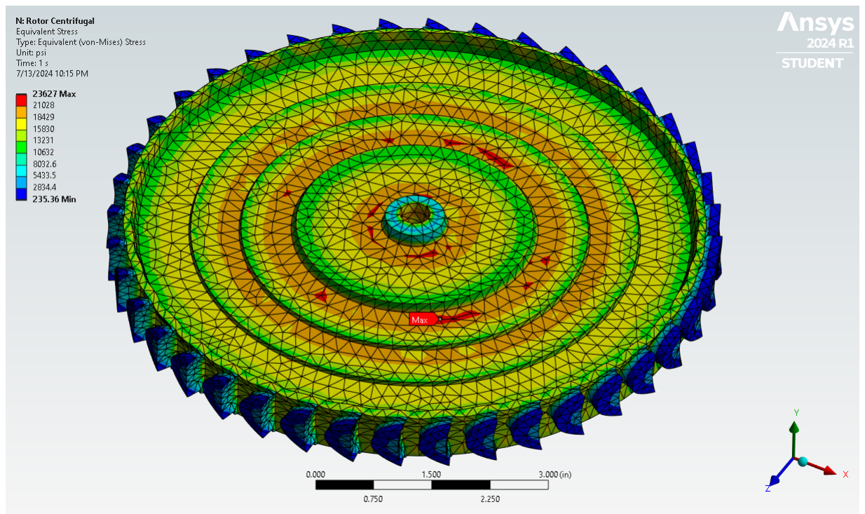
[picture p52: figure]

Figure 13: Stress on the rotor blisk. 304 stainless has an ultimate strength of appro imately 39 ksi at 1300 F.

# II. Manufacturing Process

# Impellers/Inducers

The two impellers and the two inducers were 3D printed out of aluminum using Craftcloud.com. I elected the glass blasting option but I don’t think it made much difference. The top and bottom faces of the impellers were faced off with a lathe to both increase clearance against the casing and to achieve a smoother finish.

The two impellers have a 3 mm keyway, about 10 mm long and toleranced using the ISO 286 specification. I had no issues fitting in machine keys with a snug fit that could relatively easily be assembled and disassembled by hand.

The inducers do not have keyways, simply because they would have been two deep for the geometry and made a hole rather than a groove. The fuel side inducer has two convex features on its outer shroud that nested into matching concave features on the impeller. The ox side inducer has an axial clearance hole for a 10-32 fastener that screwed into a tapped hole on the end of the pump shaft. The pump shaft is intentionally spun counter-clockwise (from the viewpoint of looking down upon the ox pump) so that the fluid reaction torque could only tighten, not loosen, this fastener.

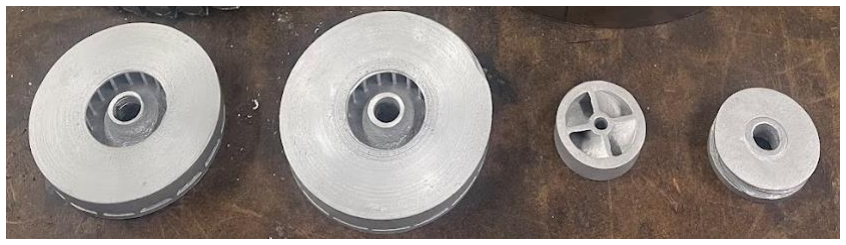
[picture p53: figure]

# Pump Casings

The ox pump has three pieces to its casing: an inboard half with an inset cavity containing the impeller and a volute channel; an upper half that mates to this; and an inlet piece on top of the upper half. The fuel pump has just two pieces: a similar inboard and outboard half (the fuel inlet is a feature integral to the outboard half) All of these pieces are 6061 aluminum, and all but one were mostly machined on a 3 axis CNC mill, then some features added on a manual lathe and/or mill. The ox inlet was done only on a manual lathe and mill.

Both halves of each pump were CNC milled out of 6” OD stock, with a square cross section spiraling outwards from the exits of the impeller channels. The ox volute was later lathed down to a final OD of 5.25” and the fuel volute to 5.75”. The fuel pump was made larger to accommodate a slightly larger impeller and volute (mostly owing to ethanol’s lower density relative to liquid oxygen; see design section). It is also larger to accommodate the turbine shaft and one of its associated bearings; the fuel pump essentially serves as the structural core for the whole turbopump. The CNC also drilled eight axial holes to fasten the halves both to each other and to the other pump and turbine manifold.

After the CNC operations, both inboard halves had a slot milled out and holes drilled to serve as the outlet. Threads were tapped to accommodate a -6 AN fitting. The fuel outboard half also had radial holes drilled to serve as the inlet, directly impinging onto the side of the fuel inducer, and threads tapped to accommodate a ½” NPT fitting. In hindsight the placement of this radial hole was a mistake and is probably most responsible for the terrible fuel pump performance relative to the ox pump. The inlet should have been designed to provide roughly axial flow onto the inducer instead; this is discussed in more detail in the test discussion section.

The ox outboard half had four holes tapped on its exterior face to mount the inlet piece. The inlet piece itself was lathed and drilled from 3” OD stock, with a ½” NPT tapped hole leading straight (axially) into a conical expanding section which led the fluid to impinge axially onto the ox impeller. In hindsight integration would have been simpler if the inlet piece was eliminated and instead the ox outboard half machined from a larger piece of stock to accommodate an integral inlet.

1/8” O-ring grooves (face seal) were also machined into the fuel inboard half, the ox outboard half, and the ox inlet. The MIL-G-5514G specification was used for tolerancing these. Grooves for the PTFE interpump spacer were lathed into the exterior faces of both inboard halves.

# Rotor

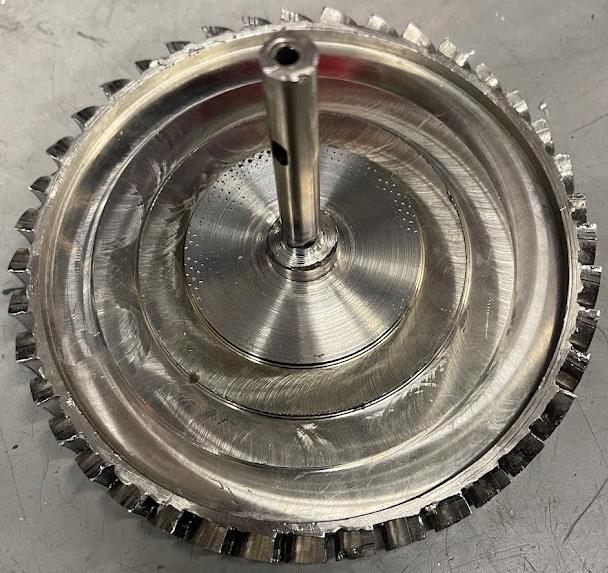
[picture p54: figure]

The turbine rotor is a single-stage, impulse driven design. It was made on a 3 axis CNC mill from 304 stainless steel. The main disk has a stepped thickness (thickest at center) to survive the centrifugal stress (more detail in analysis section). Two CNC operations were done on each face of the stock to form the main disk.

After that, the disk was mounted in a rotary table (oriented with disc normal along CNC y-axis), and then each blade milled out with a 2 mm endmill. I broke more than one endmill by milling too aggressively; but ultimately settled on a federate of 5 ipm that seemed to work well. Each blade was an approximately 12 minute operation. The rotary table was manually rotated 9 degrees between each blade operation for a total of 40 blade cuts; I did this over the course of 3 days.

# Shafts

There are two shafts: a pump shaft and a rotor shaft. Both are 10 mm OD, 303 stainless steel rotary shafts from McMaster Carr. Keyways were manually added using a mill. The pump shaft has two 3 mm keyways (for the impellers) and one 4 mm keyways (for the pump gear). The turbine shaft has a single 4 mm keyway (for the turbine gear). These were milled using 3 and 4 mm endmills, with about 0.020” passes for the 3 mm and about 0.050” passes for the 4 mm, with a <1 ipm feed rate and copious manually applied coolant. Keyways were toleranced using the ISO 286 spec.

In hindsight I would have made all keyways 4 mm and likely made the shaft 12 mm, because of the higher availability of parts (gears, bearings) that interface with that larger size.

The turbine shaft was welded to the rotor. The shaft was 303 stainless and the rotor 304 stainless. The process was TIG with ER308L filler wire. The shaft was inserted through the rotor’s central hole (press fit), sticking out about 0.1” or so on the rotor’s lower side. The welds were essentially lap joints, continuous around the circumference of the shaft, on both sides of the rotor.

More care should have been taken to ensure the shaft was precisely perpendicular to the face of the rotor. I should have created a jig setup. For external reasons I had very little time and notice to do the welding, so I made do as best I could with simple clamps.

# Turbine Housing

The turbine housing contains the gas manifold which feeds off N2 bottles in a spinflow or a GG in a hotfire. It also serves as a shroud around the rotor blades and as a structural mounting point for the primary bracket. The housing was mostly CNC machined from a single disc of 4140 cold-rolled steel, 7” OD by 1” thick. This took many hours with a a feedrate of ~5 ipm.

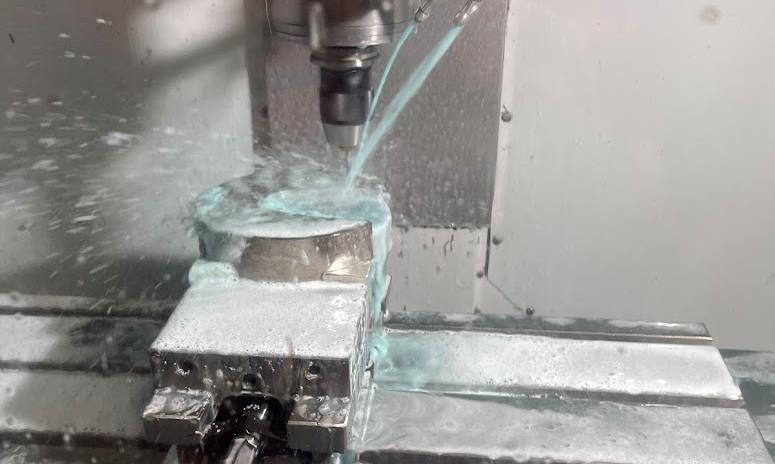
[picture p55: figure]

The gas manifold feature had a 1/8” mild steel plate welded on top to create a fully enclosed space. The process used was MIG; I would have preferred to use TIG for a cleaner weld, but a MIG was the only machine available to me the day I needed to finish this. I then welded a ½” pipe nipple vertically to it, and drilled out the central hole through the plate to create an inlet for GG gas.

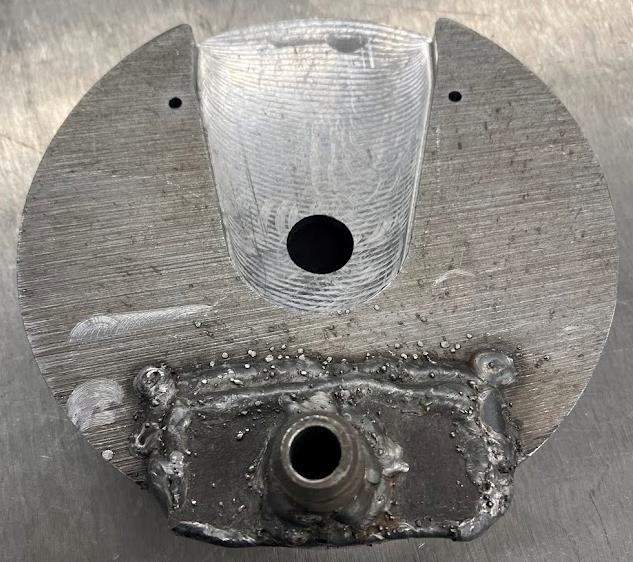
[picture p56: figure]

Three slanted holes were then drilled into the enclosed space, from the other side, and were then ground somewhat conically. This was done on a manual mill, with the head tilted by 26 degrees drilling down onto the housing which was mounted flat on a rotary table (so I could rotate between the three hole locations). These created the choked flow nozzles from which gas would leave supersonically and impinge on the rotor blades, imparting an impulse (hence the name “impulse driven rotor”). Later on, I realized that my N2 gas flow requirements had changed and it would more optimally have just two holes. So I blocked up the central hole by quite forcefully hammering a wood screw into it; I used a wood screw because it has large prominent threads that could deform into the hole to block it up.

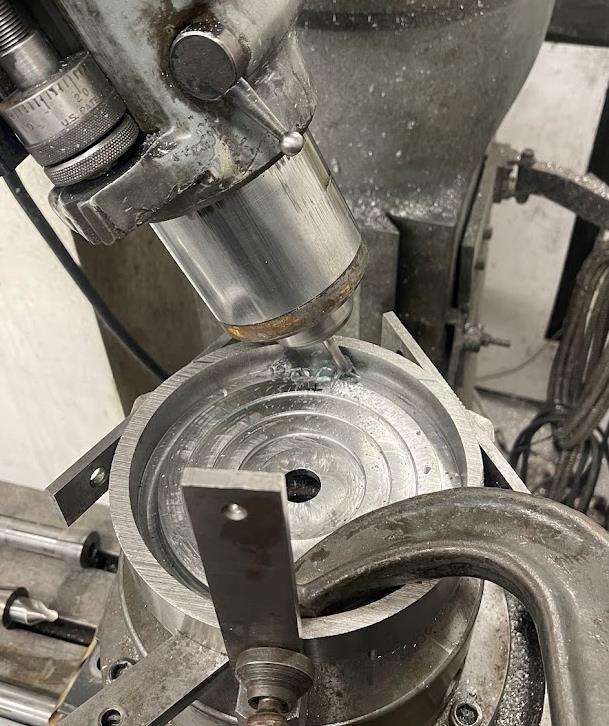
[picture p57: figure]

# III. Testing

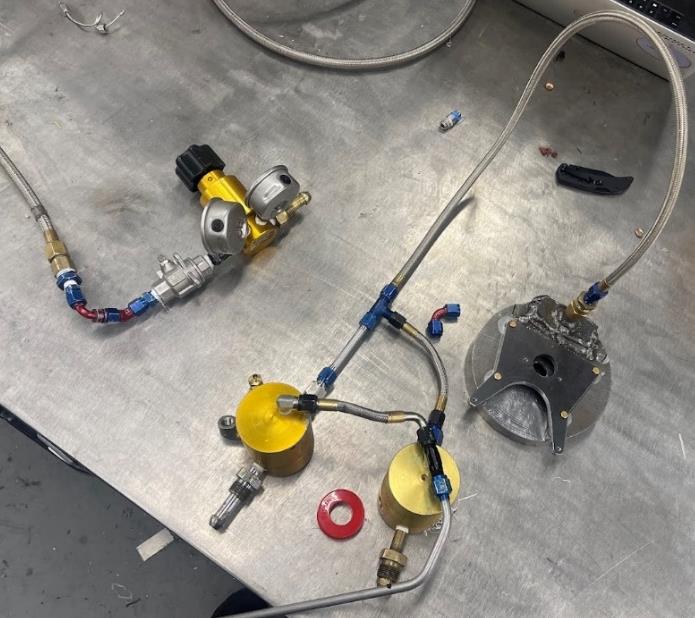
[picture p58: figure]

Nitrogen fee system. This is the only part of the project esigne by someone else; thank you to oni argousi.

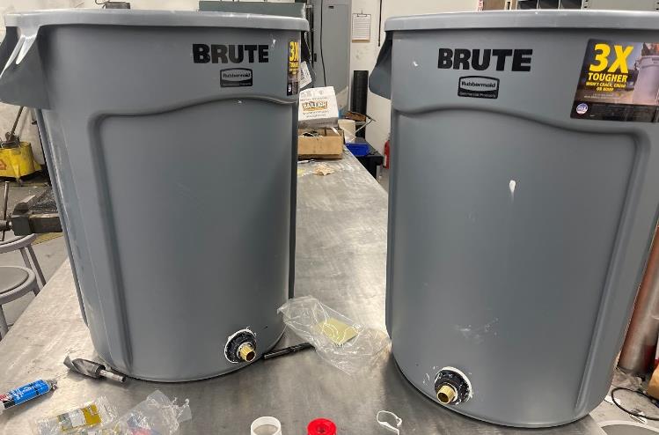
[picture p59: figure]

Two highly sophisticate water tanks for the test (one for each pump).

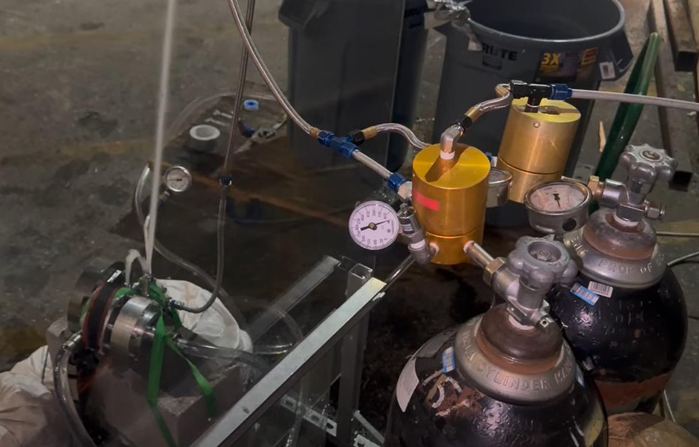
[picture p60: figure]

The feed system works by feeding off two separate nitrogen k-bottles to reach the required

## 1017 SCFM gas flow rate. There are two dome loaded pressure regulators, one on each

bottle. A third bottle has a pilot regulator on it and is used to set the pressure of the dome regulators that are actually providing gas flow for the turbine. Nitrogen flows through fle hoses into the welded inlet piece of the turbine manifold.

## Water for the is supplied from two garbage cans that I converted into large reservoirs (I bought them brand new; no trash FOD)

# First Spinflow Test (6/16/2024)

Wins and Strong Points

- The fact that it worked at all is surprising to me. I am stoked by the results of the test even though it significantly underperformed compared to the design goals.
- Little to no noticeable water leakage around any of the seals, barring a little dribbling on one side of the fuel pump. This was expected and discussed later.
- No noticeable structural damage on the pumps or turbine.
- Packing seals performed well as far as I can tell, though they should be inspected when the turbopump is taken apart later.
- Turbine seemed pretty balanced for the relatively minimal work I put in to doing so.

## Main Issues with First Test

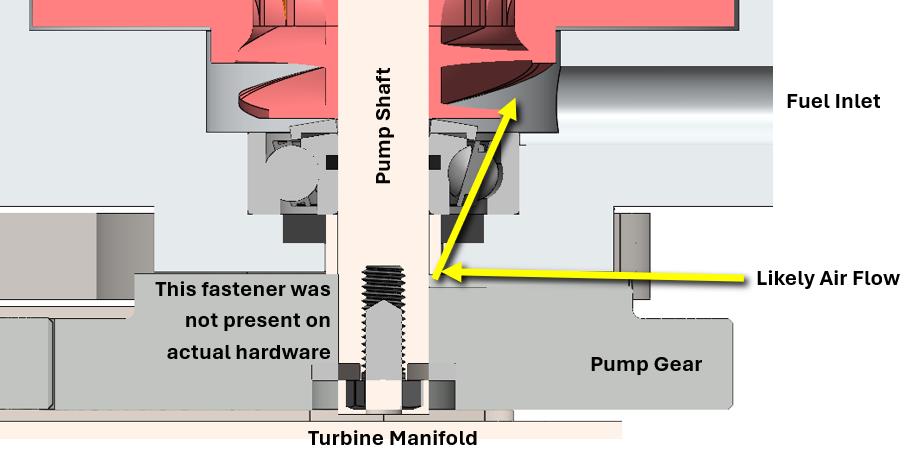
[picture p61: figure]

1) Fuel pump flow was almost nonexistent compared to lox pump. I am pretty sure this is because it was not properly sealed along its shaft, on the side close to the inlet and inducer. This is really the only relevant difference I can think of between the two pumps that could cause this. It could have been aspirating a lot of air into its inlet, more than water – maybe there was a high-pressure stream of air coming out the outlet but it’s impossible to know from the video.
My intent was to put packing seals in the pictured gap, but because it rests against the bearing it jammed the balls when I tried this; I was not able to rotate the shaft by hand at all. I opted to not put any seal at all here because of lack of time and naively hoping that the clearance between the shaft and hole was small enough to somewhat cc seal it. I knew water was going to leak out before the test started (which it did at a very slow dribble that doesn’t really affect anything), but I hadn’t thought about the fact that air would leak in during the test, in the opposite direction.
So that’s a simple design oversight – I’m thinking now I may be able to correct this by adding a small, specifically dimensioned washer of some kind that separates the bearing from the packing seals, and adding a packing seal back in. Or I may switch the open ball bearing to a sealed ball bearing and take the hit on max shaft RPM, especially since the real speed isn’t getting close anyways. This test did demonstrate that packing seals work (at least to some degree), because there was a packing seals separating the fuel and lox pumps. If they did not work then the lox pump would have been aspirating air from the fuel pump and had similarly anemic performance.

2) The first test spun great, overcoming any friction, but subsequent tests ground to a halt. We could hear (and verified from videos) that the turbine would begin spinning up for a few seconds at most and then slowed to a stop. After reapproaching, I would try to spin the turbine by hand and each time it would feel caught until I worked it around a little bit and it would start spinning freely again. Some parts (especially the gear and fuel pump casing) were slightly warmer than the other parts. To be clear, everything was quite cold from water splashing around and adiabatically expanded nitrogen gas flowing through the system (both the dome regs and nitrogen bottles were fully iced up on their surface), but those parts were close to more room temperature.
So I think it’s pretty clear the issue was a sudden spike in friction when it started spinning, and one that would not have appeared in the first test. In light of this I am pretty sure the issue is the pump gear sliding up along the shaft and coming in contact with the steel of the turbine manifold. A couple days ago I had angle grinded the pump shaft shorter and forgot to redrill and tap a bolt hole on its end which was to be used for the retention of that gear. So the gear was just friction fit axially onto the shaft (it still had a shaft key for rotation/torque so that wasn’t an issue). I didn’t fully remember this until integration was almost done, but I naively rationalized the fit was tight enough (I had to hammer it on originally, it was close to an interference fit probably) that I could leave it so I didn’t have to take it all apart and put back together (which can take hours sometimes). Last night I noticed what was originally a tight fit had gotten progressively looser from fiddling around with the system. So about an hour or so before the test, I was able to place some 5 minute epoxy on the shaft around both sides of the gear (using a 3/32” welding rod, that’s how thin the gap was). I think this epoxy job was enough for the first test to work. But because everything got quite cold and wet, the epoxy probably shattered and/or washed away at some point before the second test. Then the pump gear slid down the shaft during that test and the gear started rubbing on steel and brought the whole thing to a halt.
3) The rotation rate was way too low, so the whole system underperformed. Looking at the audio spectrum, there is a strong peak around 3750 Hz * 60 s/min * 40 blades/revolution = 5625 RPM; the target for turbine speed is 30,000 RPM (and pump speed should be 20,000 RPM). This is almost certainly mainly because the nitrogen flowrate was much too slow. Target was ~1000 SCFM, but a rough estimate of the actual rate would be 2 bottles * 230 SCF / ~2.5 min = 184 SCFM. Turbine speed is theoretically a linear function of gas mass flow, which completely tracks: 1017 SCFM / 184 SCFM * 5625 RPM = ~31000 RPM. So I think it is valid to say there is no speed problem with the turbopump itself, only the nitrogen feed to it.

I suspect the primary issue is the size of the orifice built into the bottle itself. I think it is possible a smaller effect might be a limitation of the dome reg when it gets quite cold; both regs were entirely iced up on their surface at the end of the test. I don’t think pressure loss through the feed system is a major issue because Alex did a test of this and there was very little difference between the supply reg pressure and the pressure downstream of the dome regs, and everything is a straight shot from there down to the manifold orifices without opportunity for significant losses.

# Second Spinflow Test (7/3/2024)

## The second spinflow test was more successful than the first, but only marginally so. The

fuel pump still has anemic flow. After this test is when I now think (as mentioned earlier in the report), that the larger issue with it, more than air leakage, is the direction of the

## incoming flow. The design has fluid impinging on the inducer from the side, which is then

supposed to redirect it a ially into the impeller. I no longer think it is able to effectively do this; rather the centrifugal acceleration is throwing back the incoming flow and starving the impeller of fluid.

## Correcting this problem requires a significant design overhaul, because the geometric

constraints of the current turbopump don’t allow an a ial inlet onto the fuel impeller. The

## pump gear and turbine manifold are in the way. Further work on this will require me to

redesign and remachine some parts. I do not know whether I will be doing this in the future or not, as I have now graduated and have much less time (understatement) to work on this.

## But it was a lot of fun:

# Sourcing / Tools

McMaster-Carr

Industrial Metal Supply

Home Depot

KHK Gears

Craftcloud.com – 3DPnxt and Shenzhen 3D Innovate

UCLA Machine Shop

Rocket Project at UCLA

Pierce College Welding Shop

# Helpful People

Chris Cordova – CNC training, advice, scheduling

Alex Patrus – spinflow testing, feed system setup

Roni Margousi – feed system design and setup

Adam Kajganic – some machining help

Dave Crisalli – design advice

Mario Hernandez – design advice

# References

Karassik, I., Messina, J., Cooper, P., & Heald, C. (2008). ump Han book. McGraw-Hill. NASA. (1971). Liqui ocket Engine Turbopump n ucers, S -8052.
NASA. (1973). Liqui ocket Engine Centrifugal Flow Turbopumps, S -8109.
NASA. (1974). Liqui ocket Engine Turbines, S -8110.

Also here’s me trying to cast impellers/inducers in the early days of the project. Don’t do this, the results were absolutely awful, go get these 3D printed lol (like I ultimately did through craftcloud.com).

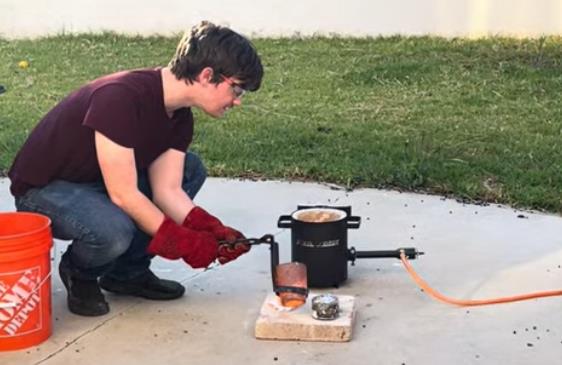
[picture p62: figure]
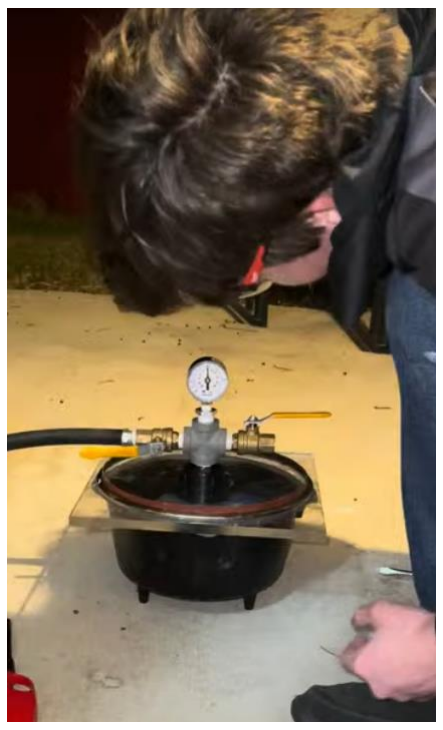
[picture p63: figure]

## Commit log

2023-07-22 pump contours
    [Impeller [TP].SLDPRT, Inducer [TP].SLDPRT, Pump Casing Cap [TP].SLDPRT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]
2023-08-17 turbopump cad
    [Impeller [TP].SLDPRT, Inducer [TP].SLDPRT, Pump Casing Cap [TP].SLDPRT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]
2024-01-22 huge cad dump
    [Efficiency_Data.xlsx, Scale Banana.SLDPRT, [TP] Main Shaft - 7405K2_316.SLDPRT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]
2024-03-04 inducer mostly finished
    [[TP] [GG] Elbow Fitting Unthreaded - 44965K412.SLDPRT, [TP] [GG] Elbow Fitting.SLDPRT, [TP] [GG] Igniter Adapter - 43455K38.SLDPRT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]
2024-04-24 kind of a ton of stuff
    [Gear Ratios.xlsx, Part1.SLDPRT, Sample Rotor 2.STEP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]
2024-05-23 big dump after computer switching fiasco
    [[TP] Pump Gear 75 Teeth - SUS1-75J10_On.sldprt, [TP] Pump to Turbine Mounting Bracket.DXF, [TP] Pump to Turbine Mounting Bracket.SLDPRT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]
2024-08-25 Final dump
    [50715K164_37 Degree Flared Fitting for Stainless Steel Tubing.SLDPRT, Gear Ratios.xlsx, Narya_RPA.cfg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]
